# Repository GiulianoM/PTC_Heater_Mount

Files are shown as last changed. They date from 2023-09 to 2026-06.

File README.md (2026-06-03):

# PTC Heater Mounting Plate for Voron 2.4 Printers
Mounting plate for a 110V 500W PTC Heater module. Fits on Voron 2.4 bed rails.

Should fit in the back of the bed, on top of the 2020 Bed Rails.

Should fit in a 250 size and above.

## NOTE THIS IS A SPICY MEATBALL

:fire:

**Do NOT ask about this in the Voron Design Discord.**

Instead, join us in [Armchair Heavy Industries](https://discord.gg/armchairengineeringsux) in [#spicy-meatball](https://discord.com/channels/1029426383614648421/1151296680168275978)

---

## Simple PTC Heater bracket.

* Plate laser cut at SendCutSend.com
* Material: 0.125" / 3.175mm 5052 Aluminum or 0.119" / 3.0mm A36/1008 Mild Steel 
* I chose Stainless Steel on my first version, and I did actually tap it with a M4 Spiral Tap with Tap Magic.

* SCS Minimum order is $29, so buy two and share with a friend.
* You can get two plates laser cut, deburred and powder coated for $30.

* Holes for the fans are sized for M4 tapping, you'll need to DIY.
* Alternatively, drill out the holes for the fans and use 4mm Self Tapping Fan Screws.
* Holes for the PTC Heater are sized for M3 3.2mm clearance, no tapping.

* Holes can also be tapped by SCS, but the price goes up a lot. 😬
* Holes on the ends are for 2020 mounting, M3 3.2mm clearance.
* Fits right on top of the bed rails for a 2.4 Voron.
* 5015 Fans so there's 5mm clearance, if you use the alternative 5032 fans you will have to add spacers or adjust otherwise.

---

### Parts List

* Spicy Meatball Plate from either:
  * [SendCutSend](https://sendcutsend.com), using the DXF drawing. I recommend steel if you're going to tap the fan holes, or have SCS tap them for you.
  * EUrobros can use https://xometry.eu/en/ for good pricing and very cheap shipping - thanks to Silvertungas for the recommendation.

* PTC Heater, 110V 500W from:
   * Amazon https://a.co/d/0az0stFU
   * Amazon https://a.co/d/3dBJtb6
   * Any 500W *Insulated* PTC heater with dimensions of 140x50x~26mm should work. 
   * 300W heaters will be too short, and won't work without some modifications.

* 2 x 5015 or 5032 axial (not blower) fan: 50x50x15mm or 50x50x32mm
  * Suggested: [Delta AFB0524HHB 24v](https://www.digikey.com/en/products/detail/delta-electronics/AFB0524HHB/2560406), $12 each (plus shipping).
  * Optional: Any from this list from Digikey: [LIST](https://www.digikey.com/en/products/filter/dc-brushless-fans-bldc/217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)
  
You want the *maximum* airflow that you can get, if possible.
5015's were chosen initially because they are only 15mm thick and fit under a 20mm extrusion with some gap.

If you have more room, use stronger fans with more airflow.

  * MAX AIRFLOW ALTERNATIVE: Delta 5032 Fans (50x50x32mm) 12V: 
    * [Delta PFB0512EHF 12V via Digikey](https://www.digikey.com/en/products/detail/delta-electronics/PFB0512EHF/9478084), $22 each (plus shipping).
    * Note that these are 12v, not 24v, and they draw *half an Amp* (540mA) each at 12v.
    * You may need something to space the plate off by 17-20mm with these thicker fans. 
  
      e.g. M5 Hollow aluminum spacers 20mm long.

      If you use M5 Hollow Aluminum Spacers, you can also drill out the four plate mounting holes and use M5 screws to mount the plate, but it's not strictly necessary.
    * Taller spacers may cause the heater to encroach above the bed area.

      Don't crash your hotend.

    * I do not recommend the printed spacers any more, they have been removed.

* M4 x 0.7 Thread Tap
  * Only if you get steel or stainless steel from SendCutSend and you intend to tap it.
 Aluminum is too thin/soft to tap well.
  * Recommended: [uxcell M4 x 0.7 Spiral Flute Tap](https://www.amazon.com/uxcell-Machine-Threading-Nitriding-Tolerance/dp/B09765XYZD)
  * Also get some tapping fluid like Tap Magic, especially for steel or stainless.
* 8 x M4 BHCS or SHCS, 20mm for the fans. Slightly longer for the Provok3d version with M4 nuts.
* 4 x M3 BHCS or SHCS, 10mm for the PTC Heater.
* 4 x M3 nuts for the PTC Heater.
* 4 x M3 screws for mounting to the bed rails:
  * 8mm for the bare plate.
  * ~ 25mm long if you're using a spacer.
  
* Recommended: Omron G3NA or G3NB SSR
* Recommended: Metal DIN Rail SSR Mount

---

### Pictures

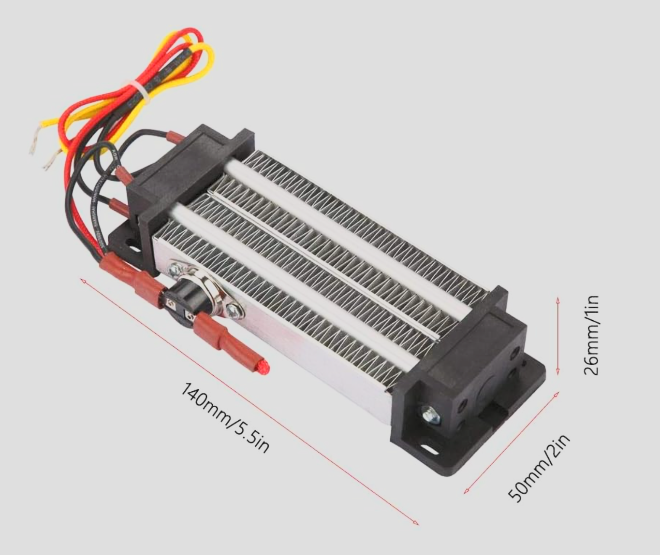
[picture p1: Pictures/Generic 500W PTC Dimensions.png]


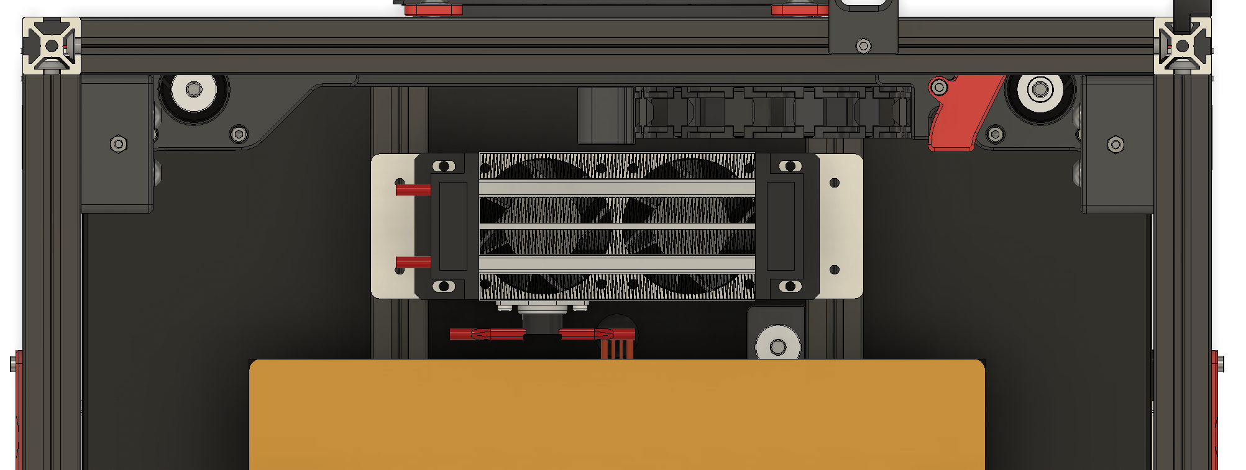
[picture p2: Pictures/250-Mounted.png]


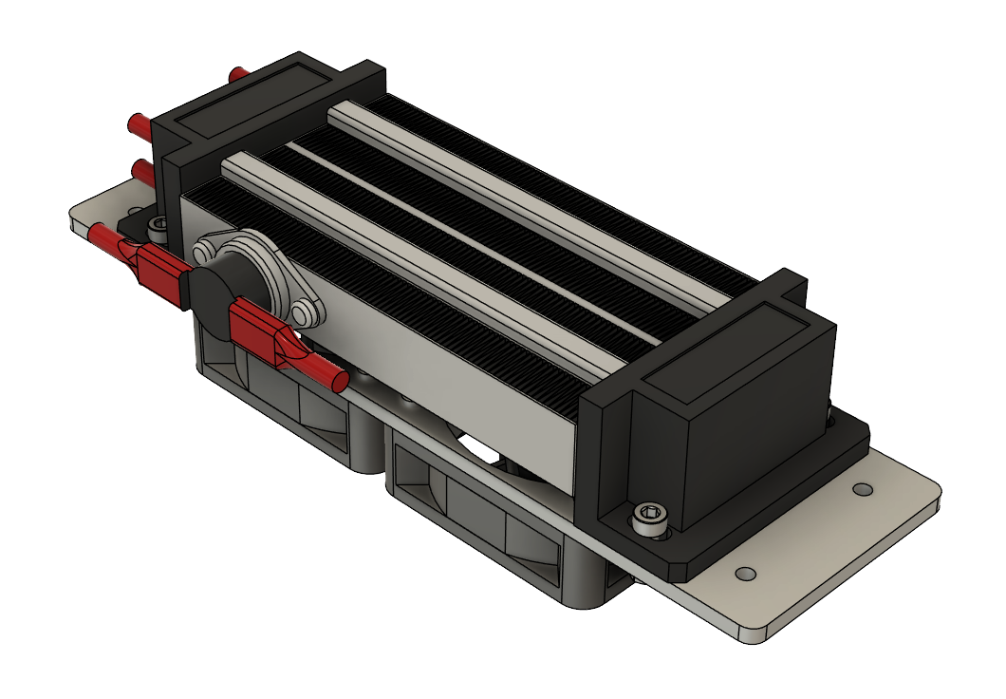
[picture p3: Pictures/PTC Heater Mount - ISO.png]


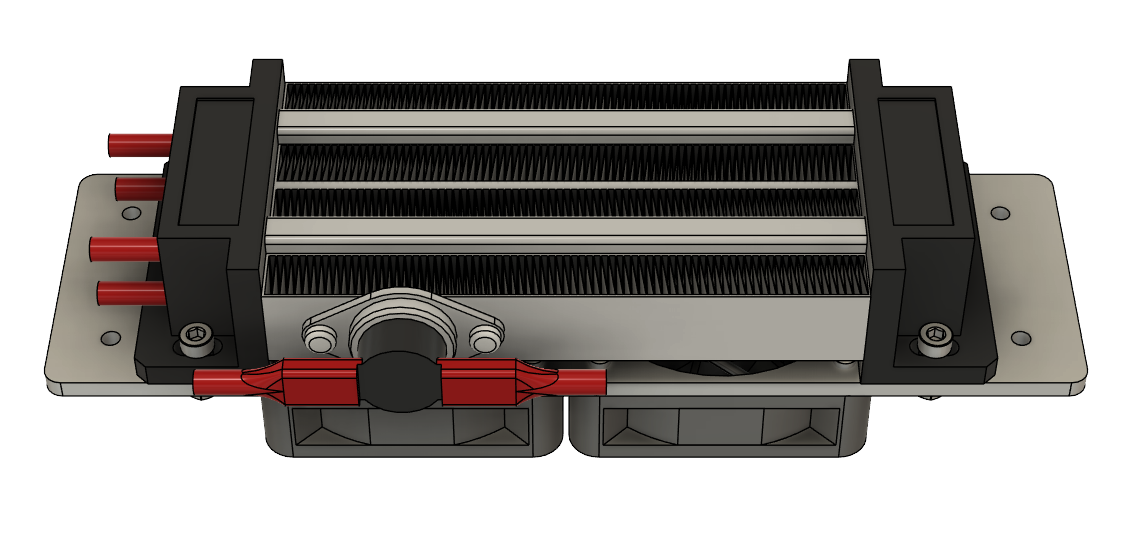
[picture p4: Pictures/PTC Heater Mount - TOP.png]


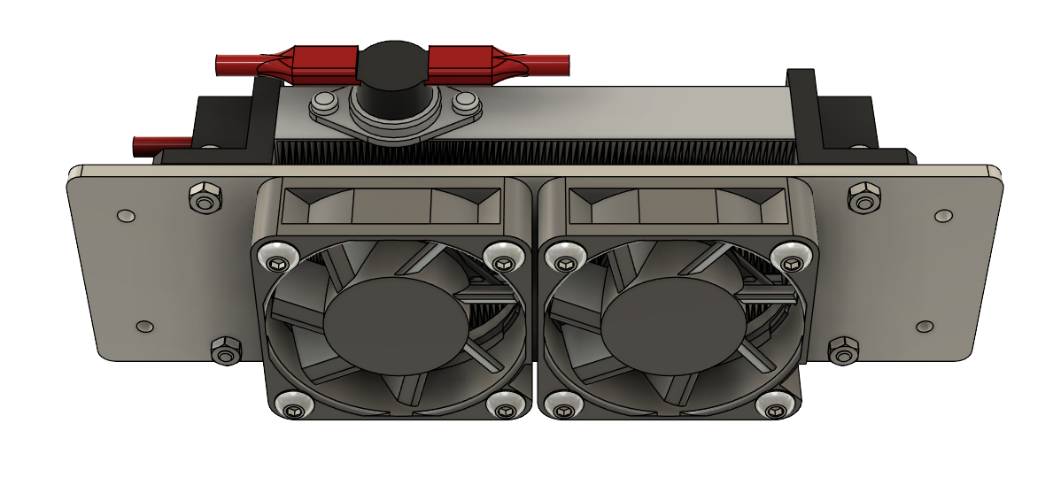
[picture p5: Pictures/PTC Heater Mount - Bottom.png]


---

## DXF File for SCS:
[PTC Heater Mount v8.DXF](/DXF/PTC%20Heater%20Mount%20v8.dxf)

Also illustration drawing: [PTC Heater Mount Drawing.PDF](/dxf/PTC%20Heater%20Mount%20Drawing.pdf) (Not for SCS)

---

<sup><sub>Please don't burn your house down.</sub></sup>

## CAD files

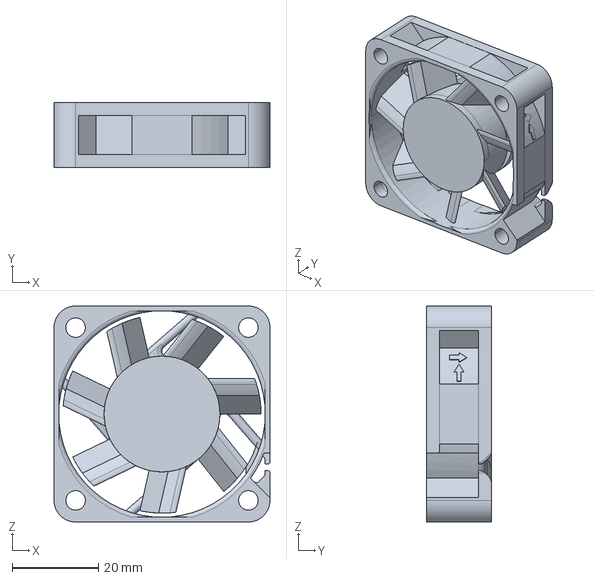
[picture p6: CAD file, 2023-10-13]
CAD/AFB0524HHB.stp
50.0 x 15.0 x 50.0 mm

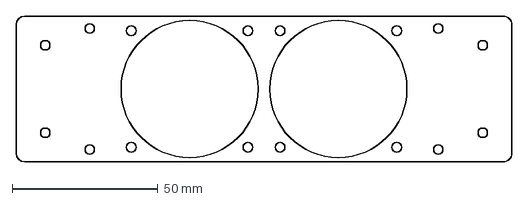
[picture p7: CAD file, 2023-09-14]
DXF/PTC Heater Mount v8.dxf
170.0 x 50.0 mm

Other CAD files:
CAD/PTC Heater Mount v8.f3z

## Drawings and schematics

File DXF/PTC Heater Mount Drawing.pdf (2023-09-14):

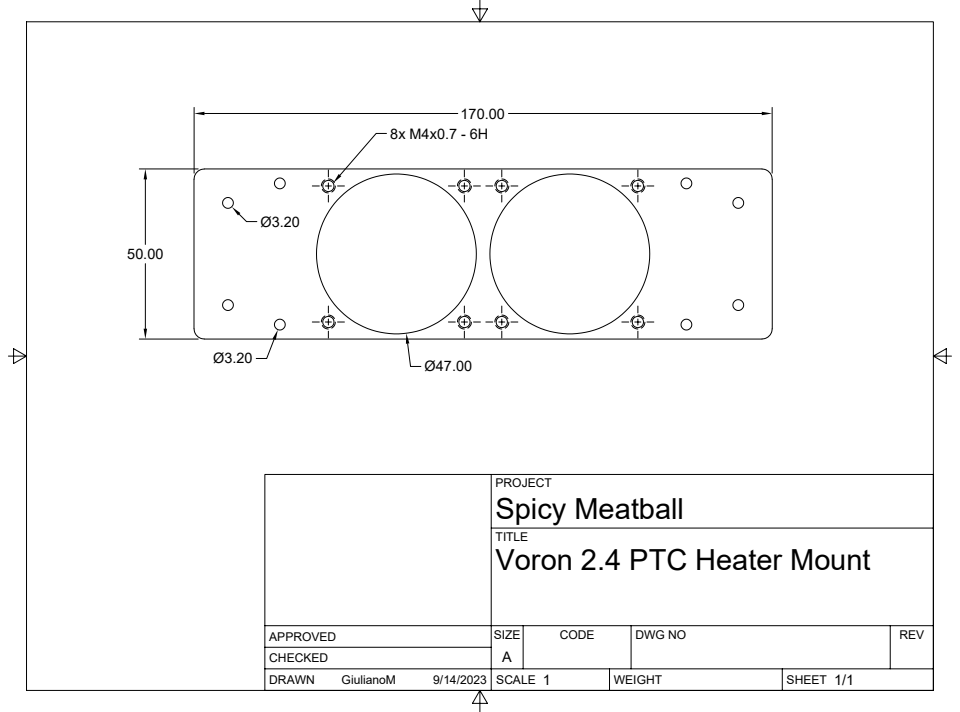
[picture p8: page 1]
PROJECT TITLE DRAWN CHECKED APPROVED; SCALE; WEIGHT; SHEET SIZE; CODE; DWG NO; REV GiulianoM; 1/1 ASpicy Meatball Voron 2.4 PTC Heater Mount ⁸x M4x0.7 - 6H 50.00

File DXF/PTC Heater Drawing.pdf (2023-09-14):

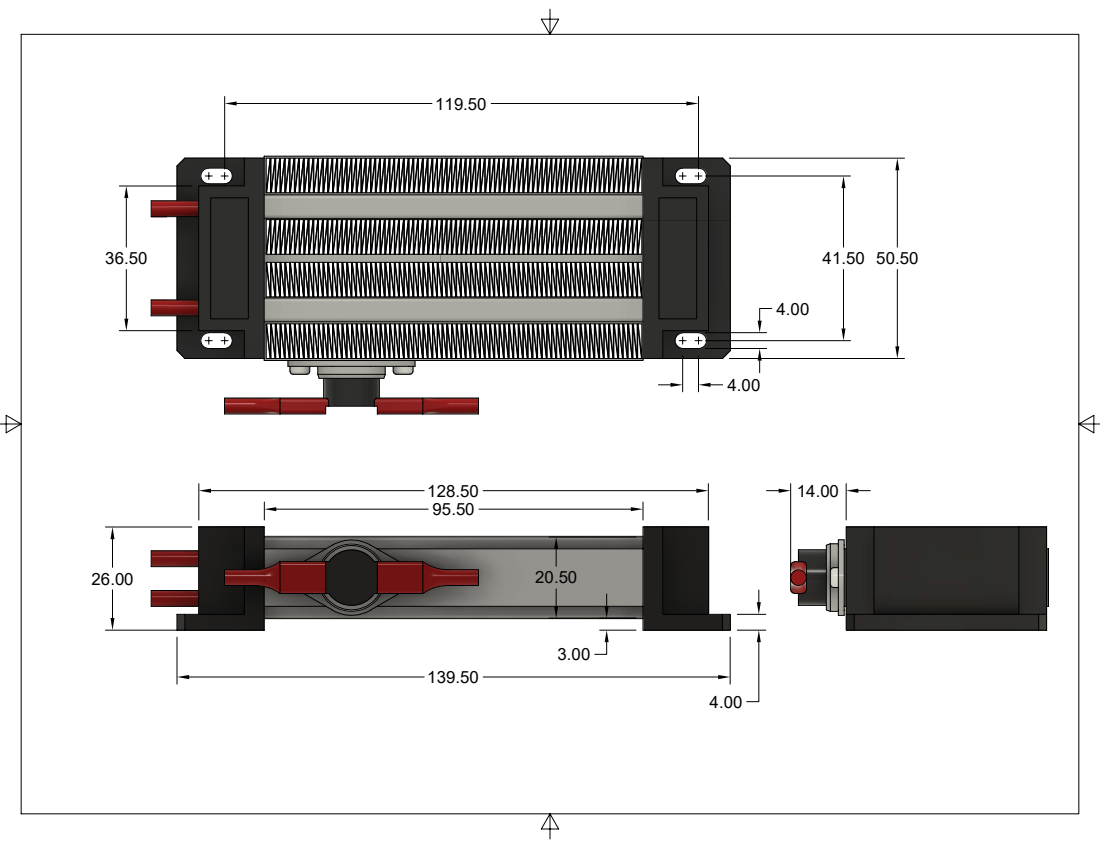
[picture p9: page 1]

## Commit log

2023-10-13 Updated CAD files
    [AFB0524HHB.stp, PTC Heater Mount v8.dxf, PTC Heater Mount v8.f3z]
2023-10-15 Updated materials
2025-01-13 Updates to docs
    Removed printed spacers, added information about 5032 fans.
    [10mm Spacer.stl, 5mm Spacer.stl]
2026-06-03 Fan updates
2026-06-03 Updated fan links
